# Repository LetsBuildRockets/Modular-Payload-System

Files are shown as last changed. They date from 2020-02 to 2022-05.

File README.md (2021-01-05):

# Cloning

This repo uses submodules. Be sure to clone the submodules as well as the repo:

```sh
git clone https://github.com/LetsBuildRockets/Modular-Payload-System/
cd Modular-Payload-System
git submodule update --init --recursive
```

# Specifications

The Modular Payload System specifications can be found [here](https://github.com/LetsBuildRockets/Modular-Payload-System/blob/master/Hardware/Reference/Specifications.md).

# Modules

A list of modules can be found [here](https://github.com/LetsBuildRockets/Modular-Payload-System/blob/master/ModuleList.md).

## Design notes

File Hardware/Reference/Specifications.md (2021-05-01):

# Modular Payload System Specifications
Revision: Draft

## Overview
These specifications are split into two categories, General Requirements that all module developers shall follow, and a following section that pertains only to modules that meet the High Reliability Requirements (HR)

## Naming Conventions

Bus modules have a basic naming scheme in the format XXX-NNM, for example CPU-010. The prefix letters define the type of module. The two numbers NN define the board number. The last number M, defines the assembly variant. 

| Prefix | Type |
| :----: | :--- |
|  PSU | Power Supply Module. Should also be used for power related modules, if for example, you needed to power external devices from the BUS rails. |
|  DBG | Debug/Development Module |
|  TOP | Top Module. Design to terminate the top of the stack. |
|  BOT | Bottom Module. Design to terminate the bottom of the stack.  |
|  CPU | Flight Computer Module |
| IO | IO board. Includes modules for driving relays, pyros, etc. |
|  BAT | Battery Module. This is any module that generates the +VBAT rail. |
|  AUX | Auxiliary Modules for doing *weird* stuff. |
|  TMP | Template Modules |

## General Specifications
1. Documentation
    1. Module naming shall conform to the naming convention outlined in this document. (This is not required for 3rd party modules, but is required if they will be contributed to LBR's repository.)
    2. Module schematics shall be licensed CC BY-NC 4.0
    3. A compliance matrix shall be filled out. A template one can be generated using by running ```python ./Scripts/generate-compliance-matrix.py ``` from the root directory of this repository. (This is not required for 3rd party modules, but is required if they will be contributed to LBR's repository.)
    4. Modules shall be labeled with a revision letter. (Follow ASME guidelines, Capitol letter A, B, C, ..., Z, AA, AB, etc. The letters I, O, P, Q, S, and Z shall be skipped)
2. Performance
    1. Electrical connectors shall have continuous current carrying capacity derated to 80%.
    2. Ceramic capacitors shall be derated to 60% operating Voltage. Partial non compliance here is acceptable if the derating failure is only due to voltage rail tolerance.
    3. Polymer tantalum capacitors shall be derated to 80% operating Voltage
    4. Polymer tantalums shall be sourced from reputable manufacturers (KEMET, AVX, etc.) No other type of polarized capacitor should be used. (The goal here is to provide safe operation for the entire bus in hot environments and at high altitudes/low pressure. Deviation from this requirement is allowed, but should be done with extreme caution)
    5. Tjmax for all ICs and discrete components should be derated to 80%
    6. All passive electrical components shall be AEC-Q200 qualified
    7. All discrete components shall be AEC-Q101 qualified
    8. All IC should be AEC-Q100 qualified. If the IC is not AEC-Q100 qualified, then it should have a pin compatible/orderable part that is AEC-Q100 qualified. (The goal here is that if the user wants to pay the extra or jump through the purchasing hurdles to actually get an AEC-Q100 part then they can, but it should be the same. For example the ATSAMC21 that is planned for this project has a AEC-Q100 qualified PN suffix, but they are non-stock. We would have to order a full reel. But by using this part, we have the option to simply order the AEC-Q100 part in the future if needed.)
    9. When digital communication and clocks greater than 25.575Mhz are used, the frequency should be chosen such that there are no odd harmonics in the L1 GPS band (1575.42 MHz  +/- 15.345 MHz). Digital frequencies keep out table included for reference below. For example, clock frequencies of 48MHz are not allow because they are between 47.275MHz and 48.205MHz and will produce a 33rd harmonic in the L1 GPS band. 48.25MHz, for example is allowed. If frequencies are used that are in the frequency keep out regions, shielding options should be evaluated in order to prevent conducted or radiated emission from interfering with GPS receivers. If an applications uses GPS other than L1, a frequency keep out table should be made by dividing the the upper and lower bandwidth limits of the band by odd divisors. See [Table 1](#table-1)
    10. Pinout
        1. J1 / P1 bus signal connector shall conform to the pinout located in [Table 4](#table-4)
        2. J2 / P2 bus power connector shall conform to the pinout locate in [Table 5](#table-5)
    11. BUS Power
        1. All power rails shall be connected to both the top and bottom bus connectors, even if the rails are unused on the module.
        2. +VBAT Rail
            1. +VBAT rail shall be 12.8VDC to 34VDC
            2. +VBAT rail steady state current shall be no more than 7.6A
            3. Total +VBAT rail transient current shall be < 1.5x max rated current of 7.6A * 1.5 =  11.4A (this includes inrush or any other transient loads, such as when radios are transmitting, etc.)
            4. Rise time shall be no faster than **TBD** V/s
            5. Rise shall be monotonic
            6. All modules that generate the +VBAT rail via switching regulator topologies shall be 100% tested to ensure conformance to operating voltage requirement. This requirement does not apply to modules that generate the +VBAT rail without active regulation and without power path components that will significantly cause a drop (or increase) in rail voltage.
        3. +12V Rail
            1. +12V rail shall be 11.2VDC to 12.6VDC
            2. +12V rail steady state current shall be no more than 4A
            3. Total +12V rail transient current shall be < 1.5x max rated current of 4A * 1.5=  6A (this includes inrush or any other transient loads, such as when radios are transmitting, etc.)
            4. +12V rail rise time shall be no faster than 10 V/ms
            5. +12V rail rise shall be monotonic
            6. All modules capable of generating the +12V rail shall be 100% tested to ensure conformance to operating voltage requirement 
        4. +5V Rail
            1. +5V rail shall be 4.85V to 5.25V
            2. +5V rail steady state current shall be no more than 3.2A
            3. Total +5V rail transient current shall be < 1.5x max rated current of 3.2A * 1.5=  4.8A (this includes inrush or any other transient loads, such as when radios are transmitting, etc.)
            4. +5V rail rise time shall be no faster than 10 V/ms
            5. +5V rail rise shall be monotonic
            6. All modules capable of generating the +5V rail shall be 100% tested to ensure conformance to operating voltage requirement
        5. +VBAT_Preboot
            1. Reference: Typically, modules don't use this rail.
            2. Reference: Loads on this net will always draw from the battery and will bypass any Under Voltage Lock Out (UVLO). This could damage the battery. Minimize loads on this rail as much as possible. For normal operation, no 3rd party module should be using this rail. Typically, the only load is the +5V_Preboot regulator.
            3. +VBAT_Preboot shall be always on when a battery/power source is connected
            4. +VBAT_Preboot rail shall be 12.8VDC to 34VDC
            5. The +VBAT_Preboot current draw shall be < 1mA (TBR)
            6. All modules capable of generating the +VBAT_Preboot rail shall be 100% tested to ensure conformance to operating voltage requirement
        6. +5V_Preboot
            1. Reference: Typically, modules don't use this rail.
            2. Reference: Loads on this net will always draw from the battery and will bypass any UVLO, which could damage the battery. Minimize loads on this rail as much as possible. For normal operation, no 3rd party module should be using this rail. Typically, the only load is the configurable inverters or active EN switches. For example, the EN switches may use a hall effect sensor that requires 5V and needs to be inverted and could be powered from this rail.
            3. +5V_Preboot shall be always on when a battery/power source is connected
            4. +5V_Preboot rail shall be 4.85V to 5.25V
            5. The +5V_Preboot current draw shall be < 3mA (**TBR**)
            6. All modules capable of generating the +5V_Preboot rail shall be 100% tested to ensure conformance to operating voltage requirement
        7. +5V_Bootstrap
            1. Reference: Typically, modules don't use this rail.
            2. Reference: The +5V_Bootstrap rail is generated by some of the power modules in order to run the microcontrollers during startup. This rail is not guaranteed to be generated by all power modules. Other modules may use this rail if they require +5V before the rest of the bus comes up.
            3. Reference: If this rail is used, it is recommended to OR the +5V_Bootstrap with +5V with diodes on the module. Typically the +5V rail has better conversion efficiency.
            4. +5V_Bootstrap rail shall be 4.85V to 5.25V
            5. The +5V_Bootstrap current draw shall be < 400mA (**TBR**). (Note some power modules my have a +5V_Bootstrap current limit of less than this, so check the datasheet of the specific power supply module you are using if you are going to load this rail.)
            6. All modules capable of generating the +5V_Preboot rail shall be 100% tested to ensure conformance to operating voltage requirement
        8. +0.9V_Reference
            1. Reference: Typically, modules don't use this rail.
            2. Reference: **TBD**
            3. +0.9V_Reference shall be **TBD** to **TBD** V
            4. The +0.9V_Reference current draw shall be < **TBD** mA
            5. All modules capable of generating the +0.9V_Reference rail shall be 100% tested to ensure conformance to operating voltage requirement
    12. BUS Signals
        1. Unused Signals:
            1. All unused signals on the bus shall be passed between J1 and P1. Otherwise the module will break the bus connections!
        2. RFU
            1. RFU, are Reserved for Future Use pins. They shall be connected between J1 and P1. This allows for the signals to be used in the future.
        3. DRAIN
            1. **TBD**
        4. CAN0
            1. **TBD**
        5. CAN1
            1. **TBD**
        6. QSPI
            1. Reference: Typically, modules don't use these signals
            2. **TBD**
            3. The QSPI nets shall be connected to both P1 and J1 to allow for the signals to pass through the module, regardless of if QSPI is used or not.
        7. I2C
            1. Reference: Typically, modules don't use these signals
            2. **TBD**
            3. The I2C nets shall be connected to both P1 and J1 to allow for the signals to pass through the module, regardless of if I2C is used or not.
        8. PPS
            1. Reference: Typically, modules don't use this signal
            2. Reference: The PPS is a precision pulse-per-second provided by GPS receivers. It is not always available on the bus. It will only be provided when there is a GPS-NNM module capable of generating this signal is on the bus, and while it has a GPS lock (or sufficient clock synchronization) 
            3. PPS shall be a one pulse per second pulse (defined by rising edge) and shall have a pulse width of 10ms to 150ms
            4. PPS must be driven through a ~680ohm series resistor.
            5. The PPS net shall be connected to both P1 and J1 to allow for the signal to pass through the module, regardless of if it is used or not.
        9. CTRL_SYNC
            1. Reference: The CTRL_SYNC is used to synchronize software loops between modules. It should be generated by a CPU_NNM module and used by the other modules to kick off their software loop. This sync signal can be divided down if required at the module.
            2. Reference: Most modules that have a microcontroller should have the CTRL_SYNC signal connected to an interrupt capable input pin.
            3. CPU_NNM modules shall output this sync signal on this net.
            4. CTRL_SYNC must be driven through a ~680ohm series resistor.
            5. The start of the control loops should be synchronized with the rising edge of the CTRL_SYNC signal.
            6. Logic high shall be 3.3V +/- 0.3V
            7. Logic low shall be < 0.4V
            8. The CTRL_SYNC frequency shall be 200Hz (**TBR**) at a duty cycle of 48% to 52%.
            9. The CTRL_SYNC net shall be connected to both P1 and J1 to allow for the signal to pass through the module, regardless of if it is used or not.
        10. EN_0, EN_1, EN_2
            1. Reference: Typically, modules don't use these signals, instead you might want to use P_GOOD to enable your module.
            2. Reference: The EN_x signals are active high discrete signals used to enable bus functionality. EN_0, when high, will enable the BAT_NNM boards to supply the +VBAT rail. This allows an external switch on rocket (i.e. a 'remove before flight' tag) to enable the avionics. EN_1 and EN_2 can be used for enabling other functionality. For example, EN_1 could be used with a logical AND gate to enable pyrotechnic charges. This allows for a separate external arming switch, so you can ground test avionics without pyros enabled.
            3. Reference:  These are 5V signals, not 3.3V logic level, so be careful not to connect them directly to a 3.3V microcontroller pin.
            4. Logic high for EN_0, EN_1 and EN_2 shall be +5V +/- 0.5V
            5. Logic low for EN_0, EN_1 and EN_2 shall be < 0.4V.
            6. The current sinked from/sourced to any of the EN_x nets shall be < 1mA.
            7. The current sinked from/sourced to any of the EN_x nets should be < 100uA per module.
            8. EN_0 should be reserved for enabling the +VBAT rail (this will bring up the +12V and +5V rails after a few ms.)
            9. EN_1 **TBD**
            10. EN_2 **TBD**
            11. The EN_0, EN_1 and EN_2 nets shall be connected to both P1 and J1 to allow for the signals to pass through the module, regardless of if it is used or not.
        11. DETECT_A/DETECT_B
             1. Reference: It is recommended that all Modules that have a microcontroller use this detect feature. See [Figure 1](#figure-1) for an example of how this detect signal could be wired up between modules.
             2. Reference: The DETECT_A and DETECT_B signals are used to autodetect the order of the Modules within a stack. This is the only signal in the bus that is not connected to all of the modules in parallel to P1 and J1. DETECT_A is only present on P1 while DETECT_B is only present on J1. DETECT_B should be configured as an input to the microcontroller with a pullup (external or internal to the microcontroller ) When this net is pulled low, the Module should identify itself on the CAN bus. The module will then drive DETECT_A low to request the next module in the stack to identify itself. The bottom board in the stack ties detect to GND to start the detect process. 
             3. If the detect signal is used in the Module, the detect net tied to J1 (top side connector) shall be called DETECT_A and the detect net tied to P1 (bottom side connector) shall be called DETECT_B.
             4. If the detect signal is used in the Module, DETECT_B shall be configured as an input with a pullup resistor between 10kohm and 500kohm to a +3.3V +/- 0.3V supply.
             5. If the detect signal is used in the Module, DETECT_A shall be configured as an open collector/drain output. It shall remain in a hi-z or pullup state (to +3.3V +/- 0.3V) until the module has finished its detect sequence, at which time it will drive the DETECT_A net low (< 0.4V).
             6. If the detect signal is not used in the Module, The net shall tie J1 to P1 and shall be called Detect.
             7. Bottom modules (BOT-NNM) shall tie DETECT_A to GND.
             8. Top modules (TOP-NNM) shall leave DETECT_B floating.
        12. P_GOOD
             1. Reference: The P_GOOD signal is intended to be to power on reset signal for the bus. It can be used to enable local 3.3V LDOs or tied to the rest pin of a microcontroller. This allows the power supplies to come up, then assert the P_GOOD signal in order to enable the rest of the modules. The P_GOOD net is driven through a 220ohm series resistor and a Schottky diode and has a 100kohm pulldown. The goal of the current requirement on this net is to keep the P_GOOD rail from sagging excessively under load. Pulldowns on every module and the Iq of any enable pin may quickly exceed the expected current on this net. The exception the current requirements is reset buttons or other reset features. P_GOOD can be tied low which will draw ~10mA, which will hold the modules in reset.
              2. Reference: Pay close attention to the input pin that P_GOOD drives. For example, if this signal is connected to an input pin of a microcontroller with an ESD diode, and the microcontroller is not powered on during the power on sequence, it could easily draw more than 1.8mA back powering the 3.3V rail.
              3. The P_GOOD signal shall be asserted to 3.3V (2.2V min. 3.6V max.) after VBAT, 12V, and 5V rails have reached operating voltage
              4. The P_GOOD signal shall be de-asserted if any of the rails fall below operating range after ~1ms of persistence
              5. The total amount of current sinked from this net shall be < 1.8 mA during operation.
              6. The total amount of current sinked per module from this net should be < 150uA during operation.
              7. The P_GOOD net shall be connected to both P1 and J1 to allow for the signal to pass through the module, regardless of if it is used or not.
3. Mechanical
    1. Connectors
        1. Top side stacking BUS connectors shall be given ref des J1 and J2 for the signal and power connectors respectively
        2. J1 and J2 shall match in part number.
        3. J1 and J2 shall be part number 10144517-061802LF, 10144517-062802LF, 10144517-063802LF, or 10144517-064802LF
        4. Bottom side stacking BUS connectors shall be given ref des P1 and P2 for the signal and power connectors respectively
        5. P1 and P2 shall be part number 10144518-064802LF
        6. If the Module uses SWD or JTAG for programming, a standard 2x5 0.05" pitch right angle box header should be used as a programming connector. This allows for consistency between modules.
        7. If the Module uses a debug UART, a S4B-ZR(LF)(SN) should be used as a debug UART connector (pin 1: +3.3V, pin 2: GND, pin 3: DEBUG_TX, pin 4: DEBUG_RX). This allows for consistency between modules.
    2. Component Height
        1. Component height limits on the top side of the board are defined by the stacking connectors. See [Table 2](#table-2)
        2. Component height limit on the bottom side of the board is 152 mil      
    3. Stack Height
        1. Reference: Module to Module stack heights are defined by the top side connector. This stack height is defined by the top side of one module to the bottom side of the module above it. i.e. not including board thickness. See [Table 3](#table-3)
    4. Board Outline
        1. Modules should be 1.750" by 1.750" with a 0.125" radius on the corners (This specification may be violated and should be evaluated on a case by case basis.)
    5. Mounting Holes
        1. Modules shall have mounting holes sized for M3 standoffs (126mil nom. drill diameter with a 218mil nom. pad diameter) located at 0.125" from the edge of the 1.75" square
    6. Board thickness
        1. Module PCBs should be 63mil nom. thickness. (This allows for the use of standard standoffs for module stacking. This specification may be violated if alternate standoffs are used)
    7. Test Points
        1. SMT test points should be at least 40mil in diameter
        2. SMT test points should be located on a 0.1" grid on the board. Per **TBD** drawing. (This allows for a standardized pogo pin test board that picks up on this grid. Save from having to create a pogo pin board for each module)
        3. SMT test points should be on top side of the board. (Bottom side test points are allowed, but will be difficult to get to within the stack!)

## High Reliability Specifications

1. Performance
    1. Switching regulators shall have a gain margin of 10dB or greater and a phase margin of 35 degrees or greater
    2. Switching regulators shall have stability performance verified by Monte-Carlo Simulation over load and over component tolerance.
    3. Switching regulators shall have stability performance verified by test at nominal load.
    4. Linear regulators shall have a phase margin of 35 degrees or greater
    5. Linear regulators shall have stability performance verified by test at nominal load.
    6. All ICs and discrete electrical components shall be analyzed to ensure TJ MAX is not exceeded under worst case conditions, or by Monte Carlo

## Tables/Figures
### Table 1
**GPS Frequency Keep outs**

| Harmonic # | Lower (MHz) | Upper (MHz) |
| :---: | :---: | :---: |
| 61 | 25.575 | 26.079 |
| 59 | 26.441 | 26.963 |
| 57 | 27.369 | 27.909 |
| 55 | 28.365 | 28.923 |
| 53 | 29.435 | 30.015 |
| 51 | 30.589 | 31.192 |
| 49 | 31.838 | 32.465 |
| 47 | 33.193 | 33.847 |
| 45 | 34.668 | 35.351 |
| 43 | 36.280 | 36.995 |
| 41 | 38.050 | 38.800 |
| 39 | 40.001 | 40.789 |
| 37 | 42.164 | 42.994 |
| 35 | 44.573 | 45.451 |
| 33 | 47.275 | 48.205 |
| 31 | 50.325 | 51.315 |
| 29 | 53.795 | 54.854 |
| 27 | 57.780 | 58.918 |
| 25 | 62.403 | 63.631 |
| 23 | 67.829 | 69.164 |
| 21 | 74.289 | 75.751 |
| 19 | 82.109 | 83.725 |
| 17 | 91.769 | 93.575 |
| 15 | 104.005 | 106.051 |
| 13 | 120.005 | 122.367 |
| 11 | 141.825 | 144.615 |
| 9 | 173.341 | 176.752 |
| 7 | 222.867 | 227.253 |
| 5 | 312.015 | 318.153 |
| 3 | 520.025 | 530.255 |
| 1 |  1560.075 |  1590.765 |

### Table 2
**Component Clearances**

| Connector PN | Top Side Component Height limit |
| :---: | :---: |
| 10144517-06**1**802LF | 152 mil |
| 10144517-06**2**802LF | 310 mil |
| 10144517-06**3**802LF | 467 mil |
| 10144517-06**4**802LF | 625 mi |

### Table 3
**Module Stack Heights**

| Connector PN | Stack Height | Recommended Standoff |
| :---: | :---: | :---: |
| 10144517-06**1**802LF | 8 mm | M2103-3005-SS |
| 10144517-06**2**802LF | 12 mm | M2107-3005-SS |
| 10144517-06**3**802LF | 16 mm | M2111-3005-SS |
| 10144517-06**4**802LF | 20 mm | M2115-3005-SS |

## Table 4

**J1 / P1 BUS Signal Connector Pinout**

| Signal | Pin # | Pin # | Signal |
| ---: | :---: | :---: | --- |
| DRAIN | 1 | 2 | DRAIN |
| RFU_3 | 3 | 4 | CAN0_N |
| RFU_5 | 5 | 6 | CAN0_N |
| RFU_5 | 7 | 8 | DRAIN |
| RFU_7 | 9 |  10 | CAN1_N |
| RFU_11 |  11 |  12 | CAN1_P |
| RFU_13 |  13 |  14 | DRAIN |
| RFU_15 |  15 |  16 | I2C_SDA |
| RFU_17 |  17 |  18 | I2C_SCL |
| RFU_19 |  19 |  20 | DRAIN |
| RFU_21 |  21 |  22 | PPS |
| RFU_23 |  23 |  24 | DRAIN |
| +5V_Preboot |  25 |  26 | CTRL_SYNC |
| DRAIN |  27 |  28 | DRAIN |
| QSPI_CLK |  29 |  30 | P_GOOD |
| QSPI_IO0 |  31 |  32 | J1: DETECT_A, P1: DETECT_B |
| QSPI_IO1 |  33 |  34 | EN_0 |
| QSPI_IO2 |  35 |  36 | EN_1 |
| QSPI_IO3 |  37 |  38 | EN_2 |
| DRAIN |  39 |  40 | DRAIN |
| SYNC_0 |  41 |  42 | +0.9V_Reference |
| GND |  43 |  44 | +5V_Bootstrap |
| GND |  45 |  46 | +5V |
| GND |  47 |  48 | +5V |
| GND |  49 |  50 | +5V |
| GND |  51 |  52 | +5V |
| GND |  53 |  54 | +5V |
| GND |  55 |  56 | +5V |
| GND |  57 |  58 | +5V |
| GND |  59 |  60 | +5V |

## Table 5

**J2 / P2 BUS Power Connector Pinout**

| Signal | Pin # | Pin # | Signal |
| ---: | :---: | :---: | --- |
| +12V | 1 | 2 | GND |
| +12V | 3 | 4 | GND |
| +12V | 5 | 6 | GND |
| +12V | 7 | 8 | GND |
| +12V | 9 |  10 | GND |
| +12V |  11 |  12 | GND |
| +12V |  13 |  14 | GND |
| +12V |  15 |  16 | GND |
| +12V |  17 |  18 | GND |
| +12V |  19 |  20 | GND |
| +VBAT |  21 |  22 | GND |
| +VBAT |  23 |  24 | GND |
| +VBAT |  25 |  26 | GND |
| +VBAT |  27 |  28 | GND |
| +VBAT |  29 |  30 | GND |
| +VBAT |  31 |  32 | GND |
| +VBAT |  33 |  34 | GND |
| +VBAT |  35 |  36 | GND |
| +VBAT |  37 |  38 | GND |
| +VBAT |  39 |  40 | GND |
| +VBAT |  41 |  42 | GND |
| +VBAT |  43 |  44 | GND |
| +VBAT |  45 |  46 | GND |
| +VBAT |  47 |  48 | GND |
| +VBAT |  49 |  50 | GND |
| +VBAT |  51 |  52 | GND |
| +VBAT |  53 |  54 | GND |
| +VBAT |  55 |  56 | GND |
| +VBAT |  57 |  58 | GND |
| +VBAT_Preboot |  59 |  60 | GND |

### Figure 1

**DETECT_A/DETECT_B Configuration**

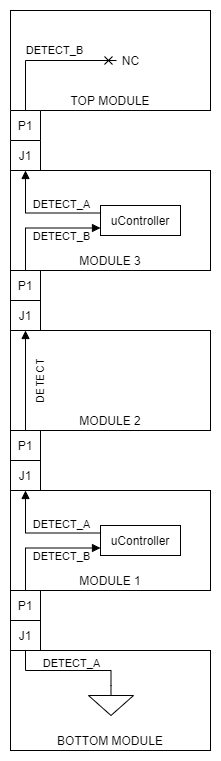
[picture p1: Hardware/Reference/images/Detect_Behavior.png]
Detect Behavior


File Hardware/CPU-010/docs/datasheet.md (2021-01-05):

# CPU-010 Debug/Development Board

## Overview
.

## Specifications
### Operating Conditions
| | Min. | Typ. | Max. | Unit |
| --- | ---- | ---- | ---- | ---- |
| +VBAT | 12.8 | 22 | 34 | V |
| +12V | 11.2 | 12 | 12.6 | V |
| +5V | 4.75 | 5 | 5.25 | V |
| +VBAT Current | | - | - | A |
| +12V Current  | | - | - | A |
| +5V Current | | - | -  | A |

## Configurations
### CPU-011

## Design Notes
### Power Consumption

| Device | PN | Min. | Typ.  | Max.  |
| :---: | :---: | :---: | :---: | :---: |
| U1 | ATSAMV71Q19B-AAB | | | 90mA  |
| U3 | ATA6561-GAQW | 0.01mA | 0.2mA | 0.5mA |
| U4 | ATA6561-GAQW | 0mA (Not in Config.) | 0.2mA | 0.5mA |
| U5 |  IS45S16800F-7TLA2 | 0mA (Not in Config.) | 80mA  | 120mA |
| U8 | KSZ8061RNBV | 0mA (Not in Config.) | | |
| X1 | | | | |
| X2 | MC2016K25.0000C16ESH | 0mA (Not in Config.) |  1mA  |  5mA  |
| SD Card<br/>e.MMC | | 0mA (Not in Config.) | 100mA | 200mA |
| | | | | |
| Total | | | | |

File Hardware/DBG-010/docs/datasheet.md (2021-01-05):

# DBG-010 Debug/Development Board

## Overview
The DBG board is design to allow for basic debug functionality for Modular Payload System (MPS)  modules.

The board provides the following functionality:
- 4mm Banana jacks for powering the bus
- An ATSAMC21G17 microcontroller, with two CAN transceivers, for developing and testing code
- Enable lines broken out (EN_0, EN_1 and EN_2)
- Various jumpers to configure P_GOOD, EN_x, +5V_Bootstrap, and +5V_Preboot

## Specifications
### Operating Conditions
| | Min. | Typ. | Max. | Unit |
| --- | ---- | ---- | ---- | ---- |
| +VBAT | 12.8 | 22 | 34 | V |
| +12V | 11.2 | 12 | 12.6 | V |
| +5V | 4.75 | 5 | 5.25 | V |
| +VBAT Current | | 0.1  | 7.6  | A |
| +12V Current  | | 0.1  | 4 | A |
| +5V Current | | 0.2  | 3.2  | A |

## Configurations
### DBG-011
This configuration has all of the functionality of the board. It has the banana jacks for powering the bus, the enable lines,  P_GOOD, two CAN transceivers, and the ATSAMC21G17.
### DBG-012
Same as DBG-010 but with P1 and P2 installed
### DBG-013
This configuration only has the banana jacks for powering the bus, the enable lines, and P_GOOD. This configuration is designed for simply providing power to the bus
### DBG-014
This configuration only has the banana jacks and top and bottom bus connectors. This configuration is designed to breakout the power connections to measure or load the rails for testing

## Jumpers
- **P5** enables generation of the +5V_Preboot rail from the +5V rail. Jumper pins 1 and 2 to enable. Jumper pins 2 and 3 to disable.
- **P6** enables generation of the +5V_Bootstrap rail from the +5V rail.  Jumper pins 1 and 2 to enable. Jumper pins 2 and 3 to disable.
- **P7** selects the EN signal for the local +3.3V LDO. Jumper pins 1 and 2 to enable the local +3.3V LDO when P_GOOD is high. This matches the functionality of most of the modules. This requires a PSU module to be present. Jumper pins 2 and 3 to enable the +3.3V LDO. Remove the jumper to disable the +3.3V LDO.
- **P21** controls the P_GOOD signal. Jumper pins 1 and 2 to force P_GOOD high. This will enable the rest of the modules on the bus. (Note, this requires the +3.3V regulator to be enabled with P7).  Jumper pins 2 and 3 to allow PSU modules to control P_GOOD. 
- **P22** controls the DETECT_B signal. Jumper pins 1 and 2 to pull DETECT_B low and start the ident process. Jumper pins 2 and 3 to leave this functionality disabled.
- **P9** enables additional termination on CAN0. Install the jumper to enable additional termination, remove the jumper to disable. This allows for somewhat proper operation of the CAN0 bus without using a TOP module.
- **P11** enables additional termination on CAN1. Install the jumper to enable additional termination, remove the jumper to disable. This allows for somewhat proper operation of the CAN1 bus without using a TOP module.
- **P12** selects the EN_0 mode. Jumper pins 1 and 2 to force EN_0 high.  Jumper pins 2 and 3 to allow the external control of EN_0 from P18. (Note, both these modes require +5V_Preboot to be present. Either enable local generation using P5, or use a PSU module)
- **P13** selects the inversion of the EN_0 signal from P18. Jumper pins 1 and 2 to use the P18 EN_0 signal. Jumper pins 2 and 3 to invert the EN_0 signal from P18.
- **P14** selects the EN_1 mode. Jumper pins 1 and 2 to force EN_1 high.  Jumper pins 2 and 3 to allow the external control of EN_1 from P19. (Note, both these modes require +5V_Preboot to be present. Either enable local generation using P5, or use a PSU module)
- **P15** selects the inversion of the EN_1 signal from P19. Jumper pins 1 and 2 to use the P19 EN_1 signal. Jumper pins 2 and 3 to invert the EN_1 signal from P19.
- **P16** selects the EN_2 mode. Jumper pins 1 and 2 to force EN_2 high.  Jumper pins 2 and 3 to allow the external control of EN_2 from P20. (Note, both these modes require +5V_Preboot to be present. Either enable local generation using P5, or use a PSU module)
- **P17** selects the inversion of the EN_2 signal from P20. Jumper pins 1 and 2 to use the P20 EN_2 signal. Jumper pins 2 and 3 to invert the EN_2 signal from P20.

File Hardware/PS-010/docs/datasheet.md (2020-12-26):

# PSU-010 Power Supply Module

## Overview
- 

## Specifications
### Operating Conditions
| | Min. | Typ. | Max. | Unit |
| --- | ---- | ---- | ---- | ---- |
| +VBAT | 12.8 | 22 | 34 | V |
| +12V | | 12 | 1 | V |
| +5V | | 5 | | V |
| +VBAT Current | | | | A |
| +12V Current  | | 0 | | A |
| +5V Current | | | | A |

## Configurations

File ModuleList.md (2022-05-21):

# Module List
|  Module | Revision | Datasheet |
|--- | --- | --- |
| ASBUILT.CSV | - | - | 
| BAT-010 - Battery Module | A (draft) | - | 
| BOB-001 | - | - | 
| CPU-010 - SAM V71 CPU Module<br/>- CPU-011 - - | A (draft) | [datasheet](https://github.com/LetsBuildRockets/Modular-Payload-System/blob/master/Hardware/CPU-010/docs/datasheet.md) | 
| CPUEX-010 - CPU Expansion<br/>- CPUEX-011 - - | A (draft) | - | 
| DBG-010 - Development/Debug Board<br/>- DBG-011 - All debug features<br/>- DBG-012 - All debug features and P1/P2<br/>- DBG-013 - Bus power and various jumpers<br/>- DBG-014 - Banana Jacks only | [A](https://github.com/LetsBuildRockets/Modular-Payload-System/releases/tag/DBG-010-A) | [datasheet](https://github.com/LetsBuildRockets/Modular-Payload-System/blob/master/Hardware/DBG-010/docs/datasheet.md) | 
| DBG-020 - Pogo Pin TP Module<br/>- DBG-021 | [A](https://github.com/LetsBuildRockets/Modular-Payload-System/releases/tag/DBG-020-A) | - | 
| DBG-030 - Pogo Pin Spacer Perf Module | [A](https://github.com/LetsBuildRockets/Modular-Payload-System/releases/tag/DBG-030-A) | - | 
| DBG-040 | - | - | 
| IO-010 | - | - | 
| PS-010 - Power Supply Module 5V/3.2A, 12V/4A<br/>- PS-011 - Power Supply Module<br/>- PS-011_SIM - Power Supply Module | [A](https://github.com/LetsBuildRockets/Modular-Payload-System/releases/tag/PS-010-A) | [datasheet](https://github.com/LetsBuildRockets/Modular-Payload-System/blob/master/Hardware/PS-010/docs/datasheet.md) | 
| TMP-010 - Modular Payload System Template<br/>- TMP-011 | [B](https://github.com/LetsBuildRockets/Modular-Payload-System/releases/tag/TMP-010-B) | - | 
| TOP-010 - Top Module | A (draft) | - | 

This file was autogenerated with /Scripts/generate-module-list.py on 05/21/2022 15:31:53

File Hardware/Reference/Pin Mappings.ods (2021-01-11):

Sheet: TMP-001
Pin(1) | I/O Pin |  |  | B(2,3) | C | D | F | G | Peripheral Assignments
SAM C21G |  | ADC0 | ADC1 | AC | SERCOM(2,3,4) | SERCOM-ALT(4) | TCC | COM | CAN | GPIO | SWD | UART
1 | PA00 |  |  |  |  | SERCOM1/ PAD[0] |  |  |  | CTRL_SYNC
2 | PA01 |  |  |  |  | SERCOM1/ PAD[1]
3 | PA02 | AIN[0] |  | AIN[4]
4 | PA03 | AIN[1] |  | AIN[5]
9 | PA04 | AIN[4] |  | AIN[0] |  | SERCOM0/ PAD[0]
10 | PA05 | AIN[5] |  | AIN[1] |  | SERCOM0/ PAD[1]
11 | PA06 | AIN[6] |  | AIN[2] |  | SERCOM0/ PAD[2]
12 | PA07 | AIN[7] |  | AIN[3] |  | SERCOM0/ PAD[3]
13 | PA08 | AIN[8] | AIN[10] |  | SERCOM0/ PAD[0] | SERCOM2/ PAD[0] | TCC1/ WO[2]
14 | PA09 | AIN[9] | AIN[11] |  | SERCOM0/ PAD[1] | SERCOM2/ PAD[1] | TCC1/ WO[3]
15 | PA10 | AIN[10] |  |  | SERCOM0/ PAD[2] | SERCOM2/ PAD[2] | TCC0/ WO[2]
16 | PA11 | AIN[11] |  |  | SERCOM0/ PAD[3] | SERCOM2/ PAD[3] | TCC0/ WO[3]
21 | PA12 |  |  |  | SERCOM2/ PAD[0] | SERCOM4/ PAD[0] | TCC0/ WO[6] |  |  | DETECT_A
22 | PA13 |  |  |  | SERCOM2/ PAD[1] | SERCOM4/ PAD[1] | TCC0/ WO[7] |  |  | DETECT_B
23 | PA14 |  |  |  | SERCOM2/ PAD[2] | SERCOM4/ PAD[2] | TCC0/ WO[4] |  |  | XTAL
24 | PA15 |  |  |  | SERCOM2/ PAD[3] | SERCOM4/ PAD[3] | TCC0/ WO[5] |  |  | XTAL_NC
25 | PA16 |  |  |  | SERCOM1/ PAD[0] | SERCOM3/ PAD[0] | TCC0/ WO[6] |  |  |  |  | DEBUG_TX
26 | PA17 |  |  |  | SERCOM1/ PAD[1] | SERCOM3/ PAD[1] | TCC0/ WO[7] |  |  |  |  | DEBUG_RX
27 | PA18 |  |  |  | SERCOM1/ PAD[2] | SERCOM3/ PAD[2] | TCC0/ WO[2]
28 | PA19 |  |  |  | SERCOM1/ PAD[3] | SERCOM3/ PAD[3] | TCC0/ WO[3]
29 | PA20 |  |  |  | SERCOM5/ PAD[2] | SERCOM3/ PAD[2] | TCC0/ WO[6]
30 | PA21 |  |  |  | SERCOM5/ PAD[3] | SERCOM3/ PAD[3] | TCC0/ WO[7]
31 | PA22 |  |  |  | SERCOM3/ PAD[0] | SERCOM5/ PAD[0] | TCC0/ WO[4]
32 | PA23 |  |  |  | SERCOM3/ PAD[1] | SERCOM5/ PAD[1] | TCC0/ WO[5]
33 | PA24 |  |  |  | SERCOM3/ PAD[2] | SERCOM5/ PAD[2] | TCC1/ WO[2] | CAN0/TX
34 | PA25 |  |  |  | SERCOM3/ PAD[3] | SERCOM5/ PAD[3] | TCC1/ WO[3] | CAN0/RX
39 | PA27
41 | PA28 |  |  |  |  |  |  |  | CAN0_STBY
45 | PA30 |  |  |  |  | SERCOM1/ PAD[2] |  | CORTEX_M0P/ SWCLK |  |  | SWCLK
46 | PA31 |  |  |  |  | SERCOM1/ PAD[3] |  | CORTEX_M0P/ SWDIO |  |  | SWDIO
47 | PB02 |  | AIN[2] |  |  | SERCOM5/ PAD[0]
48 | PB03 |  | AIN[3] |  |  | SERCOM5/ PAD[1]
7 | PB08 | AIN[2] | AIN[4] |  |  | SERCOM4/ PAD[0]
8 | PB09 | AIN[3] | AIN[5] |  |  | SERCOM4/ PAD[1]
19 | PB10 |  |  |  |  | SERCOM4/ PAD[2] | TCC0/ WO[4] | CAN1/TX
20 | PB11 |  |  |  |  | SERCOM4/ PAD[3] | TCC0/ WO[5] | CAN1/RX
37 | PB22 |  |  |  |  | SERCOM5/ PAD[2] |  | CAN0/TX | CAN0_TX
38 | PB23 |  |  |  |  | SERCOM5/ PAD[3] |  | CAN0/RX | CAN0_RX

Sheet: IO-001
Pin(1) | I/O Pin |  |  | B(2,3) | C | D | G | Peripheral Assignments
SAM C21G |  | ADC0 | ADC1 | AC | SERCOM(2,3,4) | SERCOM-ALT(4) | COM | CAN | Analog | GPIO | SWD
1 | PA00 |  |  |  |  | SERCOM1/ PAD[0]
2 | PA01 |  |  |  |  | SERCOM1/ PAD[1]
3 | PA02 | AIN[0] |  | AIN[4]
4 | PA03 | AIN[1] |  | AIN[5]
9 | PA04 | AIN[4] |  | AIN[0] |  | SERCOM0/ PAD[0]
10 | PA05 | AIN[5] |  | AIN[1] |  | SERCOM0/ PAD[1]
11 | PA06 | AIN[6] |  | AIN[2] |  | SERCOM0/ PAD[2]
12 | PA07 | AIN[7] |  | AIN[3] |  | SERCOM0/ PAD[3]
13 | PA08 | AIN[8] | AIN[10] |  | SERCOM0/ PAD[0] | SERCOM2/ PAD[0]
14 | PA09 | AIN[9] | AIN[11] |  | SERCOM0/ PAD[1] | SERCOM2/ PAD[1]
15 | PA10 | AIN[10] |  |  | SERCOM0/ PAD[2] | SERCOM2/ PAD[2]
16 | PA11 | AIN[11] |  |  | SERCOM0/ PAD[3] | SERCOM2/ PAD[3]
21 | PA12 |  |  |  | SERCOM2/ PAD[0] | SERCOM4/ PAD[0]
22 | PA13 |  |  |  | SERCOM2/ PAD[1] | SERCOM4/ PAD[1] |  |  |  | DETECT_A
23 | PA14 |  |  |  | SERCOM2/ PAD[2] | SERCOM4/ PAD[2] |  |  |  | DETECT_B
24 | PA15 |  |  |  | SERCOM2/ PAD[3] | SERCOM4/ PAD[3]
25 | PA16 |  |  |  | SERCOM1/ PAD[0] | SERCOM3/ PAD[0]
26 | PA17 |  |  |  | SERCOM1/ PAD[1] | SERCOM3/ PAD[1]
27 | PA18 |  |  |  | SERCOM1/ PAD[2] | SERCOM3/ PAD[2]
28 | PA19 |  |  |  | SERCOM1/ PAD[3] | SERCOM3/ PAD[3]
29 | PA20 |  |  |  | SERCOM5/ PAD[2] | SERCOM3/ PAD[2]
30 | PA21 |  |  |  | SERCOM5/ PAD[3] | SERCOM3/ PAD[3]
31 | PA22 |  |  |  | SERCOM3/ PAD[0] | SERCOM5/ PAD[0]
32 | PA23 |  |  |  | SERCOM3/ PAD[1] | SERCOM5/ PAD[1]
33 | PA24 |  |  |  | SERCOM3/ PAD[2] | SERCOM5/ PAD[2] | CAN0/TX | CAN0TX
34 | PA25 |  |  |  | SERCOM3/ PAD[3] | SERCOM5/ PAD[3] | CAN0/RX | CAN0RX
39 | PA27 |  |  |  |  |  |  | CAN0_STBY
41 | PA28 |  |  |  |  |  |  | CAN1_STBY
45 | PA30 |  |  |  |  | SERCOM1/ PAD[2] | CORTEX_M0P/ SWCLK |  |  |  | SWCLK
46 | PA31 |  |  |  |  | SERCOM1/ PAD[3] | CORTEX_M0P/ SWDIO |  |  |  | SWDIO
47 | PB02 |  | AIN[2] |  |  | SERCOM5/ PAD[0]
48 | PB03 |  | AIN[3] |  |  | SERCOM5/ PAD[1]
7 | PB08 | AIN[2] | AIN[4] |  |  | SERCOM4/ PAD[0]
8 | PB09 | AIN[3] | AIN[5] |  |  | SERCOM4/ PAD[1]
19 | PB10 |  |  |  |  | SERCOM4/ PAD[2] | CAN1/TX | CAN1TX
20 | PB11 |  |  |  |  | SERCOM4/ PAD[3] | CAN1/RX | CAN1RX
37 | PB22 |  |  |  |  | SERCOM5/ PAD[2] | CAN0/TX
38 | PB23 |  |  |  |  | SERCOM5/ PAD[3] | CAN0/RX

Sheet: DBG-010
Pin(1) | I/O Pin |  |  | B(2,3) | C | D | G | Peripheral Assignments
SAM C21G |  | ADC0 | ADC1 | AC | SERCOM(2,3,4) | SERCOM-ALT(4) | COM | CAN | Analog | GPIO | SWD | I2C | SPI | UART
1 | PA00 |  |  |  |  | SERCOM1/ PAD[0] |  |  |  | CTRL_SYNC
2 | PA01 |  |  |  |  | SERCOM1/ PAD[1]
3 | PA02 | AIN[0] |  | AIN[4]
4 | PA03 | AIN[1] |  | AIN[5]
9 | PA04 | AIN[4] |  | AIN[0] |  | SERCOM0/ PAD[0] |  |  |  |  |  |  |  | UART_TX
10 | PA05 | AIN[5] |  | AIN[1] |  | SERCOM0/ PAD[1] |  |  |  |  |  |  |  | UART_RX
11 | PA06 | AIN[6] |  | AIN[2] |  | SERCOM0/ PAD[2]
12 | PA07 | AIN[7] |  | AIN[3] |  | SERCOM0/ PAD[3]
13 | PA08 | AIN[8] | AIN[10] |  | SERCOM0/ PAD[0] | SERCOM2/ PAD[0] |  |  |  |  |  |  | SPI_MISO_R
14 | PA09 | AIN[9] | AIN[11] |  | SERCOM0/ PAD[1] | SERCOM2/ PAD[1]
15 | PA10 | AIN[10] |  |  | SERCOM0/ PAD[2] | SERCOM2/ PAD[2] |  |  |  |  |  |  | SPI_MOSI_R
16 | PA11 | AIN[11] |  |  | SERCOM0/ PAD[3] | SERCOM2/ PAD[3] |  |  |  |  |  |  | SPI_SCK_R
21 | PA12 |  |  |  | SERCOM2/ PAD[0] | SERCOM4/ PAD[0] |  |  |  | DETECT_A
22 | PA13 |  |  |  | SERCOM2/ PAD[1] | SERCOM4/ PAD[1] |  |  |  | DETECT_B
23 | PA14 |  |  |  | SERCOM2/ PAD[2] | SERCOM4/ PAD[2] |  |  |  | XTAL
24 | PA15 |  |  |  | SERCOM2/ PAD[3] | SERCOM4/ PAD[3] |  |  |  | XTAL_NC
25 | PA16 |  |  |  | SERCOM1/ PAD[0] | SERCOM3/ PAD[0] |  |  |  |  |  | I2C_SDA
26 | PA17 |  |  |  | SERCOM1/ PAD[1] | SERCOM3/ PAD[1] |  |  |  |  |  | I2C_SCL
27 | PA18 |  |  |  | SERCOM1/ PAD[2] | SERCOM3/ PAD[2] |  |  |  |  |  |  |  | DEBUG_TX
28 | PA19 |  |  |  | SERCOM1/ PAD[3] | SERCOM3/ PAD[3] |  |  |  |  |  |  |  | DEBUG_RX
29 | PA20 |  |  |  | SERCOM5/ PAD[2] | SERCOM3/ PAD[2]
30 | PA21 |  |  |  | SERCOM5/ PAD[3] | SERCOM3/ PAD[3]
31 | PA22 |  |  |  | SERCOM3/ PAD[0] | SERCOM5/ PAD[0]
32 | PA23 |  |  |  | SERCOM3/ PAD[1] | SERCOM5/ PAD[1]
33 | PA24 |  |  |  | SERCOM3/ PAD[2] | SERCOM5/ PAD[2] | CAN0/TX
34 | PA25 |  |  |  | SERCOM3/ PAD[3] | SERCOM5/ PAD[3] | CAN0/RX
39 | PA27 |  |  |  |  |  |  | CAN1_STBY
41 | PA28 |  |  |  |  |  |  | CAN0_STBY
45 | PA30 |  |  |  |  | SERCOM1/ PAD[2] | CORTEX_M0P/ SWCLK |  |  |  | SWCLK
46 | PA31 |  |  |  |  | SERCOM1/ PAD[3] | CORTEX_M0P/ SWDIO |  |  |  | SWDIO
47 | PB02 |  | AIN[2] |  |  | SERCOM5/ PAD[0]
48 | PB03 |  | AIN[3] |  |  | SERCOM5/ PAD[1]
7 | PB08 | AIN[2] | AIN[4] |  |  | SERCOM4/ PAD[0]
8 | PB09 | AIN[3] | AIN[5] |  |  | SERCOM4/ PAD[1]
19 | PB10 |  |  |  |  | SERCOM4/ PAD[2] | CAN1/TX | CAN1TX
20 | PB11 |  |  |  |  | SERCOM4/ PAD[3] | CAN1/RX | CAN1RX
37 | PB22 |  |  |  |  | SERCOM5/ PAD[2] | CAN0/TX | CAN0TX
38 | PB23 |  |  |  |  | SERCOM5/ PAD[3] | CAN0/RX | CAN0RX
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

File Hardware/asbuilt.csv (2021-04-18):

Part Number | Revision | SN | as built changes
PS-011 | A | 1 | R13, R23 – ERJ-3EKF1004V instead of ERJ-PB6B1004V U3 – ATA6561-GAQW-N instead of ATA6561-GAQW

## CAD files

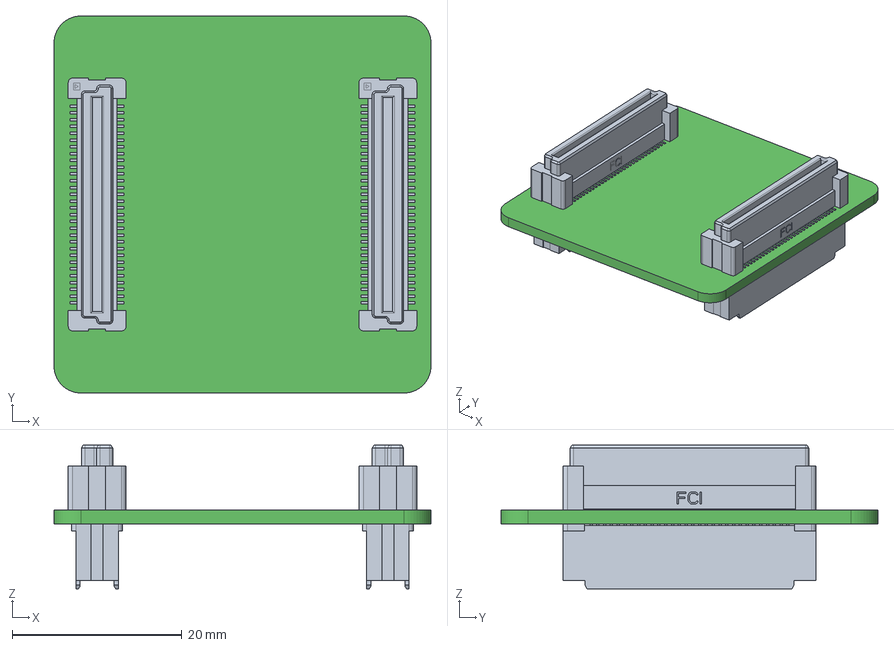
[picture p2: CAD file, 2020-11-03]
Hardware/DBG-040/Sources/Outputs/ExportSTEP/DBG-040.step
44.4 x 44.4 x 16.9 mm
Board
10144518-064x0xxx x 2
10144517-062x0xxx x 2

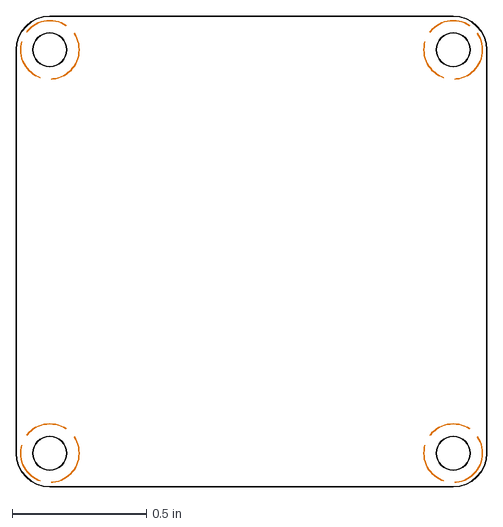
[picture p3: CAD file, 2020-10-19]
Hardware/Reference/Outline.dxf
1.75 x 1.75 in

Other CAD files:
Hardware/Reference/Outline.ipt

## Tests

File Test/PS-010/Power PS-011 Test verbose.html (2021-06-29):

In [1]:

import numpy as np
import time
from ds1054z import DS1054Z
%matplotlib inline
import matplotlib.pyplot as plt
from scipy.signal import blackmanharris
from matplotlib.ticker import EngFormatter
from scipy import signal
from IPython.display import Markdown, display

scope = DS1054Z('192.168.1.252')
print(scope.idn)

def printmd(string, color=None):
    if color != None:
        string = "<span style='color:{}'>{}</span>".format(color, string)
    display(Markdown(string))

RIGOL TECHNOLOGIES,DS1054Z,DS1ZA192409533,00.04.04.SP3

In [2]:

def check_monotonicity_rise(time_data, voltage_data, threshold, window_len_0=301, window_len_1=901):
    voltage_data_filtered = signal.savgol_filter(voltage_data, window_length=window_len_0, polyorder=2, delta=(time_data[1]-time_data[0]))
    fig, ax = plt.subplots()
    ax.plot(time_data, voltage_data) 
    ax.plot(time_data, voltage_data_filtered) 
    formatter = EngFormatter(unit='s')
    ax.xaxis.set_major_formatter(formatter)
    plt.xlabel('Time')
    plt.ylabel('Volts')
    
    dvdt = signal.savgol_filter(voltage_data, window_length=window_len_1, polyorder=2, deriv=1, delta=(time_data[1]-time_data[0]))*1e-3

    fig, ax = plt.subplots(2,figsize=(10,8), dpi=100)
    nmon = dvdt < threshold
    errors_x = []
    errors_y = []
    for x in range(0,len(nmon)):
        if nmon[x]:
            errors_x.append(time_data[x])
            errors_y.append(voltage_data_filtered[x])

    ax[0].plot(errors_x,errors_y,'.', color='lightcoral', markersize=20) 
    ax[0].plot(time_data,voltage_data_filtered)
    ax[0].set(ylabel='Volts')
    ax[1].axhline(threshold, color='lightcoral')
    ax[1].plot(time_data,dvdt) 
    ax[1].set(ylabel='Volts/ms')
    formatter = EngFormatter(unit='s')
    ax[0].xaxis.set_major_formatter(formatter)
    ax[1].xaxis.set_major_formatter(formatter)
    plt.xlabel('Time')
    
    return min(dvdt)

In [3]:

reqnum = '2.11.4.5'
printmd("### {}".format(reqnum))
printmd("**Checking {} - +5V rail rise shall be monotonic**".format(reqnum))
print("Setting up scope for checking rising monotonicity...")
scope.run()
scope.display_only_channel(1)
scope.set_probe_ratio(1,1)
scope.memory_depth = 120e3
scope.timebase_scale = 1e-3
scope.timebase_offset = 0
scope.set_channel_scale(1,1)
scope.set_channel_offset(1,-3)
scope.write(':TRIGger:MODE EDGE')
scope.write(':TRIGger:COUPling DC')
scope.write(':TRIGger:EDGe:SOURce CHANnel1')
scope.write(':TRIGger:EDGe:SLOPe POSitive')
scope.write(':TRIGger:EDGe:LEVel 2.5')
scope.single()
time.sleep(1)
print("Scope setup. Waiting for trigger.")
while(scope.running):
    time.sleep(1)
print("Triggered!")

print("Grabbing scope data...")
V1 = scope.get_waveform_samples(1,mode='MAX')
Ts1 = scope.waveform_time_values
print("Grabbed scope data!")

monotonic_threshold = -0.5 # V/ms

minimum_slew = check_monotonicity_rise(Ts1, V1, threshold=monotonic_threshold)

print('Maximum Negative slew is {:.2f} V/ms'.format(minimum_slew))

if(minimum_slew > monotonic_threshold):
    printmd('{} - PASSED'.format(reqnum), color='Green')
else:
    printmd('{} - FAILED'.format(reqnum), color='Red')

plt.show()

### 2.11.4.5¶

Checking 2.11.4.5 - +5V rail rise shall be monotonic

Setting up scope for checking rising monotonicity...
Scope setup. Waiting for trigger.
Triggered!
Grabbing scope data...
Grabbed scope data!
Maximum Negative slew is -0.12 V/ms

2.11.4.5 - PASSED

In [4]:

reqnum = '2.11.4.4'
printmd("### {}".format(reqnum))
printmd("**Checking 2.11.4.4 - +5V rail rise time shall be no faster than 10 V/ms**")
rise_slew_rate = float(scope.query(':MEASure:ITEM? PSLEWrate,CHANnel1'))
print('+5V Rail rise slew rate is {:.1f} V/s'.format(rise_slew_rate))
if(minimum_slew < 10e3):
    printmd('{} - PASSED'.format(reqnum), color='Green')
else:
    printmd('{} - FAILED'.format(reqnum), color='Red')

### 2.11.4.4¶

Checking 2.11.4.4 - +5V rail rise time shall be no faster than 10 V/ms

+5V Rail rise slew rate is 1186.8 V/s

2.11.4.4 - PASSED

In [5]:

reqnum = '2.11.3.5'
printmd('### {}'.format(reqnum))
printmd("**Checking {}- +12V rail rise shall be monotonic**".format(reqnum))
print("Setting up scope for checking rising monotonicity...")
scope.run()
scope.display_only_channel(1)
scope.set_probe_ratio(1,1)
scope.memory_depth = 120e3
scope.timebase_scale = 1e-3
scope.timebase_offset = 0
scope.set_channel_scale(1,2)
scope.set_channel_offset(1,-6)
scope.write(':TRIGger:MODE EDGE')
scope.write(':TRIGger:COUPling DC')
scope.write(':TRIGger:EDGe:SOURce CHANnel1')
scope.write(':TRIGger:EDGe:SLOPe POSitive')
scope.write(':TRIGger:EDGe:LEVel 5')
scope.single()
time.sleep(1)
print("Scope setup. Waiting for trigger.")
while(scope.running):
    time.sleep(1)
print("Triggered!")

print("Grabbing scope data...")
V1 = scope.get_waveform_samples(1,mode='MAX')
Ts1 = scope.waveform_time_values
print("Grabbed scope data!")

monotonic_threshold = -0.5 # V/ms

minimum_slew = check_monotonicity_rise(Ts1, V1, threshold=monotonic_threshold)

print('Maximum Negative slew is {:.2f} V/ms'.format(minimum_slew))

if(minimum_slew > monotonic_threshold):
    printmd('{} - PASSED'.format(reqnum), color='Green')
else:
    printmd('{} - FAILED'.format(reqnum), color='Red')

plt.show()

### 2.11.3.5¶

Checking 2.11.3.5- +12V rail rise shall be monotonic

Setting up scope for checking rising monotonicity...
Scope setup. Waiting for trigger.
Triggered!
Grabbing scope data...
Grabbed scope data!
Maximum Negative slew is -0.24 V/ms

2.11.3.5 - PASSED

In [6]:

reqnum = '2.11.3.4'
printmd('### {}'.format(reqnum))
printmd('**Checking {} - +12V rail rise time shall be no faster than 10 V/ms**'.format(reqnum))
rise_slew_rate = float(scope.query(':MEASure:ITEM? PSLEWrate,CHANnel1'))
print('+12V Rail rise slew rate is {:.1f} V/s'.format(rise_slew_rate))
if(minimum_slew < 10e3):
    printmd('{} - PASSED'.format(reqnum), color='Green')
else:
    printmd('{} - FAILED'.format(reqnum), color='Red')

### 2.11.3.4¶

Checking 2.11.3.4 - +12V rail rise time shall be no faster than 10 V/ms

+12V Rail rise slew rate is 2753.6 V/s

2.11.3.4 - PASSED

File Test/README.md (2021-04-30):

generate report using: ``` jupyter nbconvert --to pdf --no-input [notebook].ipynb```

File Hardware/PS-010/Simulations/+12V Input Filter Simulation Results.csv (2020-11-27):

fr | qf | z_out
7.56E+04 | 1.31E+00 | 1.36E-01
8.46E+04 | 1.25E+00 | 1.41E-01
7.55E+04 | 1.23E+00 | 1.44E-01
9.52E+04 | 1.20E+00 | 1.42E-01
7.23E+04 | 1.23E+00 | 1.41E-01
1.14E+05 | 1.14E+00 | 1.34E-01
6.60E+04 | 1.21E+00 | 1.52E-01
8.14E+04 | 1.18E+00 | 1.46E-01
9.08E+04 | 1.09E+00 | 1.61E-01
7.90E+04 | 1.09E+00 | 1.61E-01
6.59E+04 | 1.37E+00 | 1.27E-01
1.09E+05 | 1.26E+00 | 1.28E-01
9.10E+04 | 1.23E+00 | 1.39E-01
6.90E+04 | 1.24E+00 | 1.52E-01
6.59E+04 | 1.18E+00 | 1.62E-01
1.15E+05 | 1.17E+00 | 1.32E-01
7.57E+04 | 1.24E+00 | 1.47E-01
7.93E+04 | 1.20E+00 | 1.47E-01
1.15E+05 | 1.07E+00 | 1.49E-01
1.14E+05 | 1.08E+00 | 1.52E-01
9.10E+04 | 1.27E+00 | 1.30E-01
8.70E+04 | 1.28E+00 | 1.28E-01
7.55E+04 | 1.29E+00 | 1.36E-01
7.93E+04 | 1.27E+00 | 1.46E-01
1.03E+05 | 1.15E+00 | 1.33E-01
7.56E+04 | 1.16E+00 | 1.53E-01
8.68E+04 | 1.12E+00 | 1.52E-01
7.22E+04 | 1.14E+00 | 1.60E-01
9.38E+04 | 1.10E+00 | 1.55E-01
9.55E+04 | 1.07E+00 | 1.53E-01
9.94E+04 | 1.27E+00 | 1.25E-01
7.58E+04 | 1.33E+00 | 1.33E-01
7.90E+04 | 1.30E+00 | 1.31E-01
7.24E+04 | 1.28E+00 | 1.36E-01
6.59E+04 | 1.23E+00 | 1.43E-01
6.57E+04 | 1.20E+00 | 1.56E-01
1.04E+05 | 1.17E+00 | 1.41E-01
1.20E+05 | 1.09E+00 | 1.50E-01
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

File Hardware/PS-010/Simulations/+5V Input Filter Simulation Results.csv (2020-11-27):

fr | qf | z_out
5.24E+04 | 1.33E+00 | 1.63E-01
6.41E+04 | 1.30E+00 | 1.50E-01
7.06E+04 | 1.23E+00 | 1.60E-01
5.74E+04 | 1.21E+00 | 1.79E-01
5.99E+04 | 1.31E+00 | 1.60E-01
6.43E+04 | 1.17E+00 | 1.78E-01
7.54E+04 | 1.09E+00 | 1.77E-01
6.28E+04 | 1.12E+00 | 1.85E-01
6.55E+04 | 1.09E+00 | 1.94E-01
5.60E+04 | 1.14E+00 | 1.86E-01
5.87E+04 | 1.28E+00 | 1.58E-01
7.88E+04 | 1.23E+00 | 1.53E-01
7.71E+04 | 1.22E+00 | 1.59E-01
5.72E+04 | 1.27E+00 | 1.60E-01
6.00E+04 | 1.21E+00 | 1.64E-01
6.43E+04 | 1.16E+00 | 1.88E-01
5.72E+04 | 1.22E+00 | 1.77E-01
5.48E+04 | 1.21E+00 | 1.75E-01
7.73E+04 | 1.11E+00 | 1.72E-01
6.70E+04 | 1.07E+00 | 2.00E-01
6.86E+04 | 1.28E+00 | 1.52E-01
5.73E+04 | 1.25E+00 | 1.76E-01
6.70E+04 | 1.19E+00 | 1.69E-01
5.56E+04 | 1.28E+00 | 1.57E-01
5.48E+04 | 1.23E+00 | 1.61E-01
6.88E+04 | 1.17E+00 | 1.72E-01
5.84E+04 | 1.16E+00 | 1.79E-01
5.86E+04 | 1.19E+00 | 1.80E-01
5.36E+04 | 1.18E+00 | 1.83E-01
6.05E+04 | 1.08E+00 | 1.85E-01
6.41E+04 | 1.29E+00 | 1.56E-01
5.46E+04 | 1.27E+00 | 1.67E-01
5.74E+04 | 1.23E+00 | 1.73E-01
6.74E+04 | 1.24E+00 | 1.54E-01
5.87E+04 | 1.25E+00 | 1.67E-01
7.19E+04 | 1.12E+00 | 1.75E-01
7.56E+04 | 1.15E+00 | 1.68E-01
7.37E+04 | 1.11E+00 | 1.72E-01
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

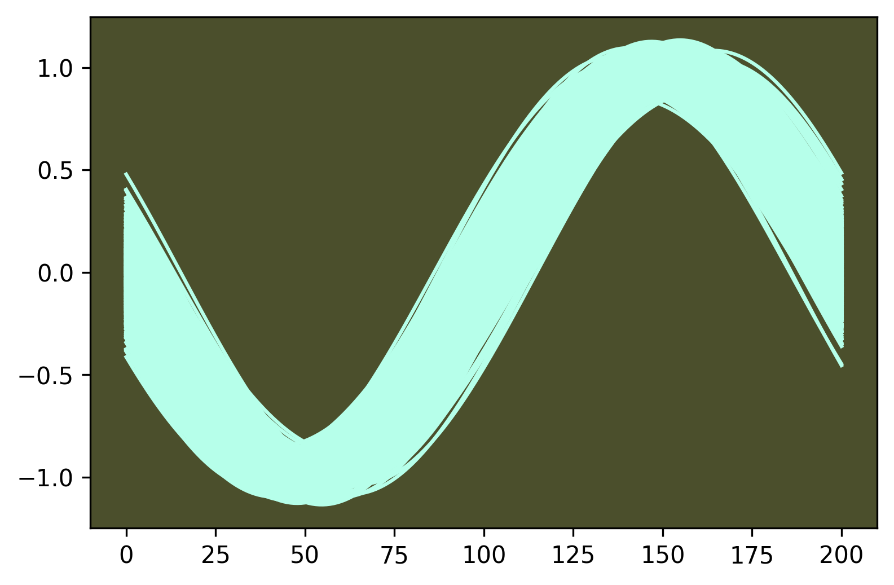
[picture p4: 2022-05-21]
Test/testbench/INST_Drivers/pandas_m.png

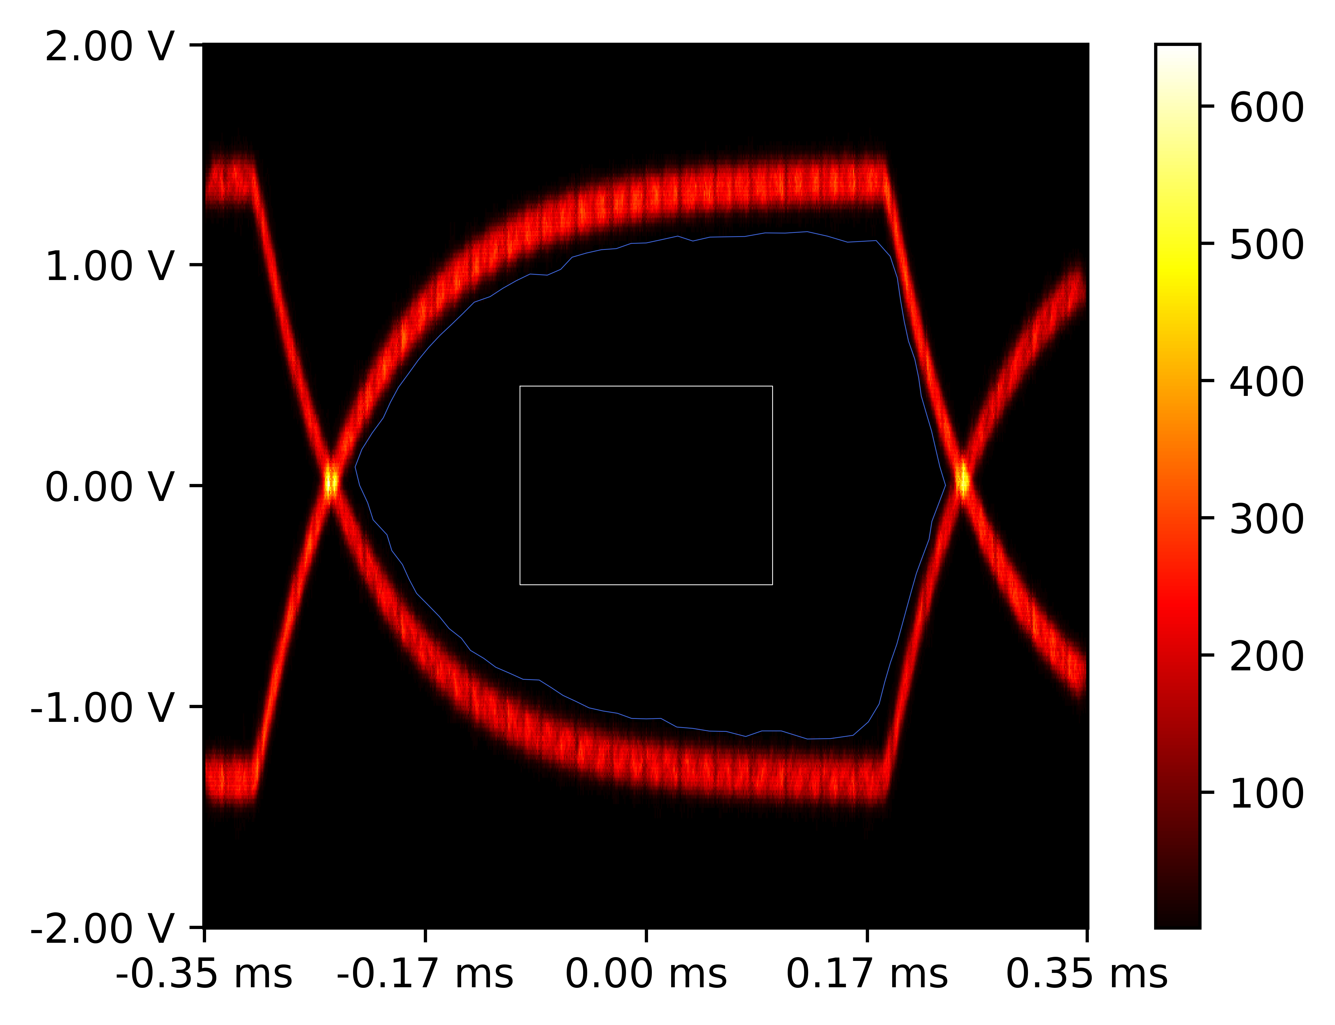
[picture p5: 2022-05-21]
Test/testbench/INST_Drivers/hand_made_persistence.png

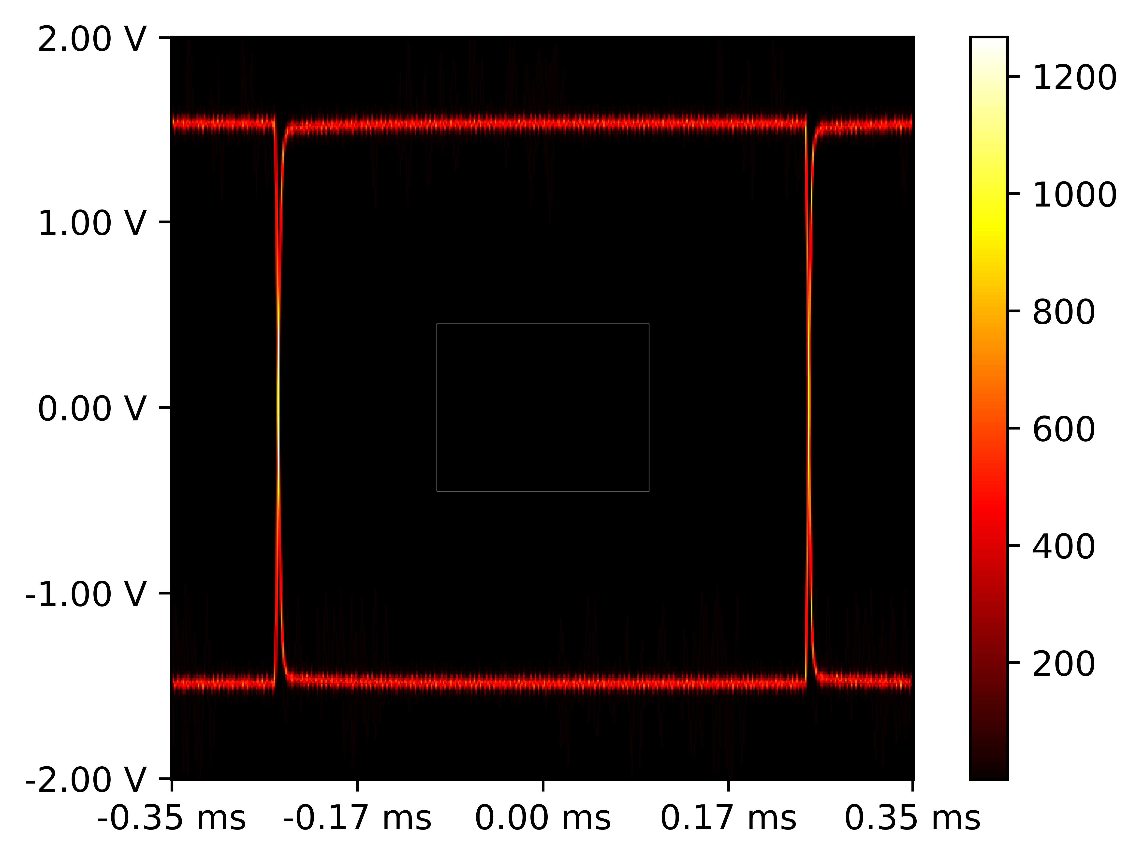
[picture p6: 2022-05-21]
Test/testbench/INST_Drivers/hand_made_persistence - Copy (2).png

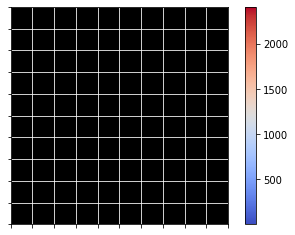
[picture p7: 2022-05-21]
Test/testbench/INST_Drivers/eye-diagram.png

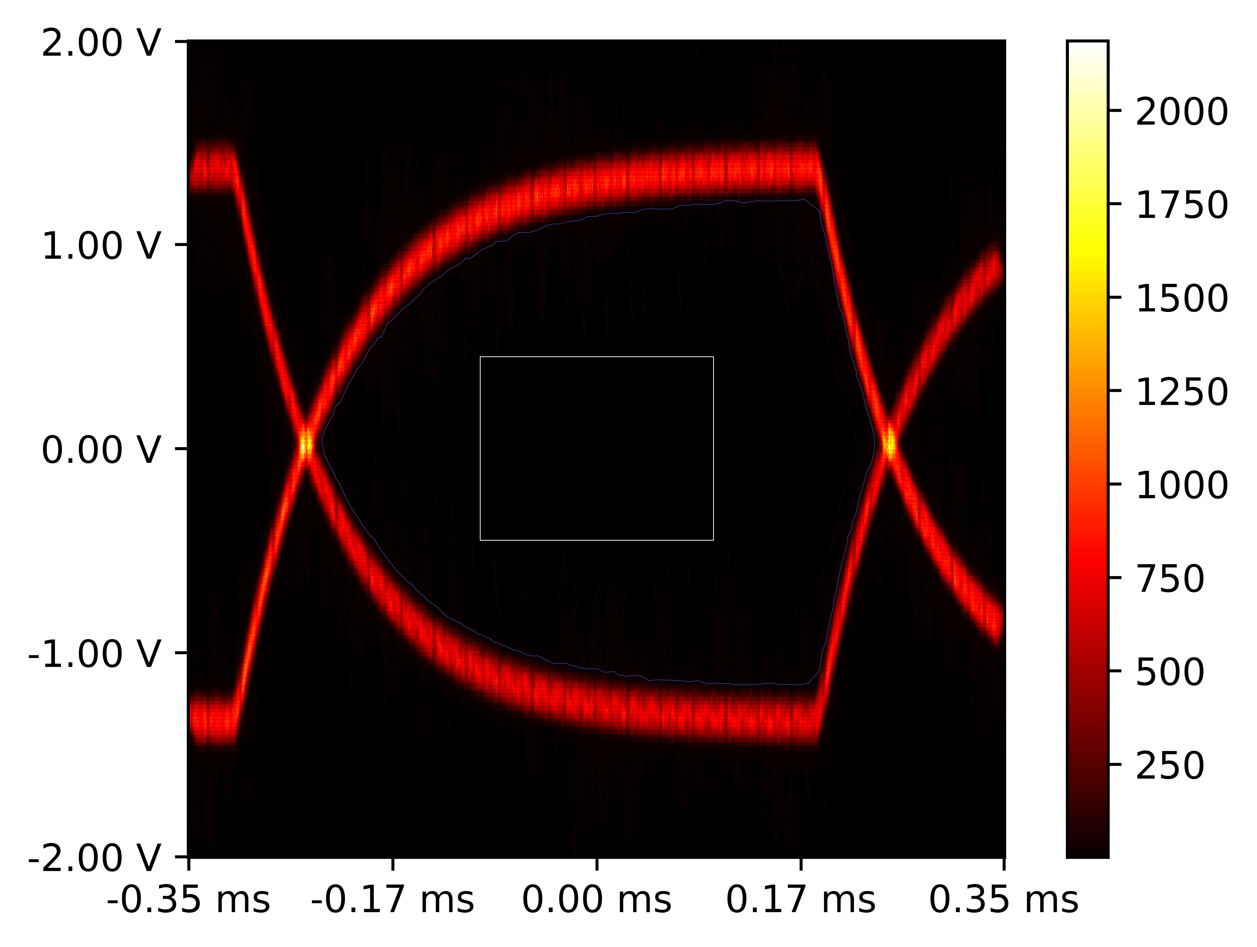
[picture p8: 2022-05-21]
Test/testbench/INST_Drivers/eye.png

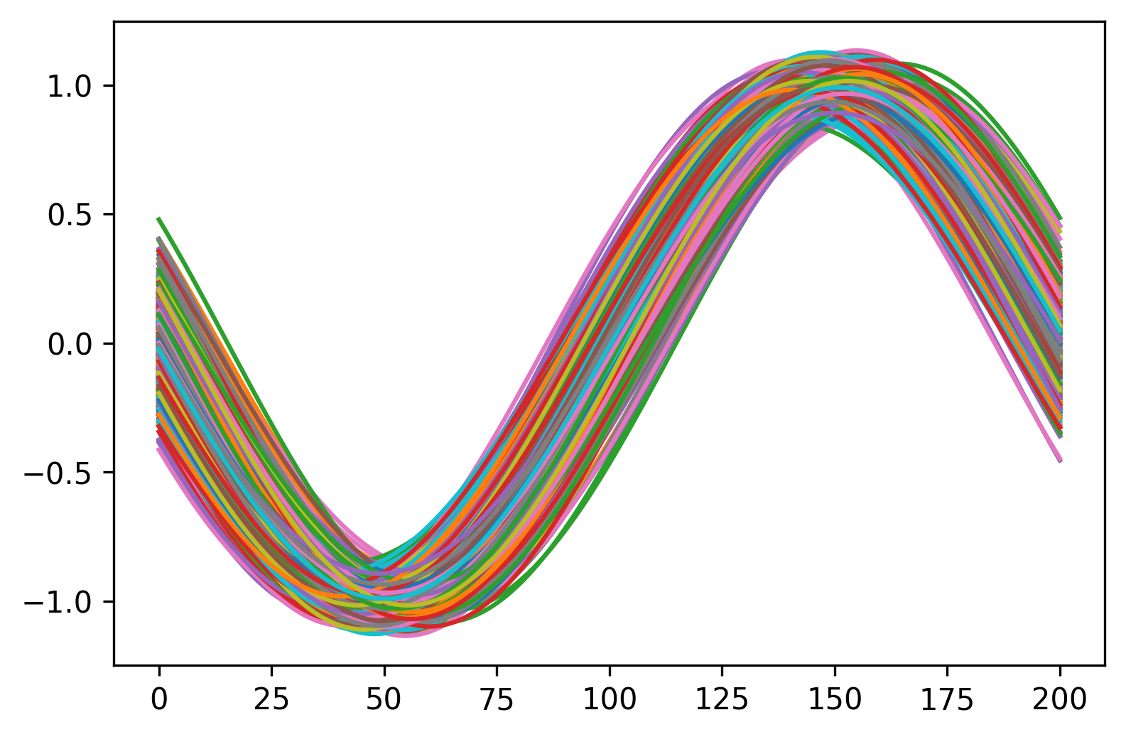
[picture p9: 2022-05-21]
Test/testbench/INST_Drivers/pandas.png

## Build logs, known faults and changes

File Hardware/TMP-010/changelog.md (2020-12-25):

# TMP-010 Change Log

## A.1

- Initial Release

## B

- Changed from Circuit studio to Altium
- Added variants
- Changed naming from TMP-001 to TMP-010, where first two digits represent the board number, and the last is the assembly variant
- Updated title block to include variants and template version
- Changed project parameters to start with the Project prefix
- Updated PNs to incude full orderable PN
- **Updated component height clearances**
- **Changed RFU_25 to +5V_Preboot rail**
- **Renamed +VBAT_Bootstrap to +VBAT_Preboot**

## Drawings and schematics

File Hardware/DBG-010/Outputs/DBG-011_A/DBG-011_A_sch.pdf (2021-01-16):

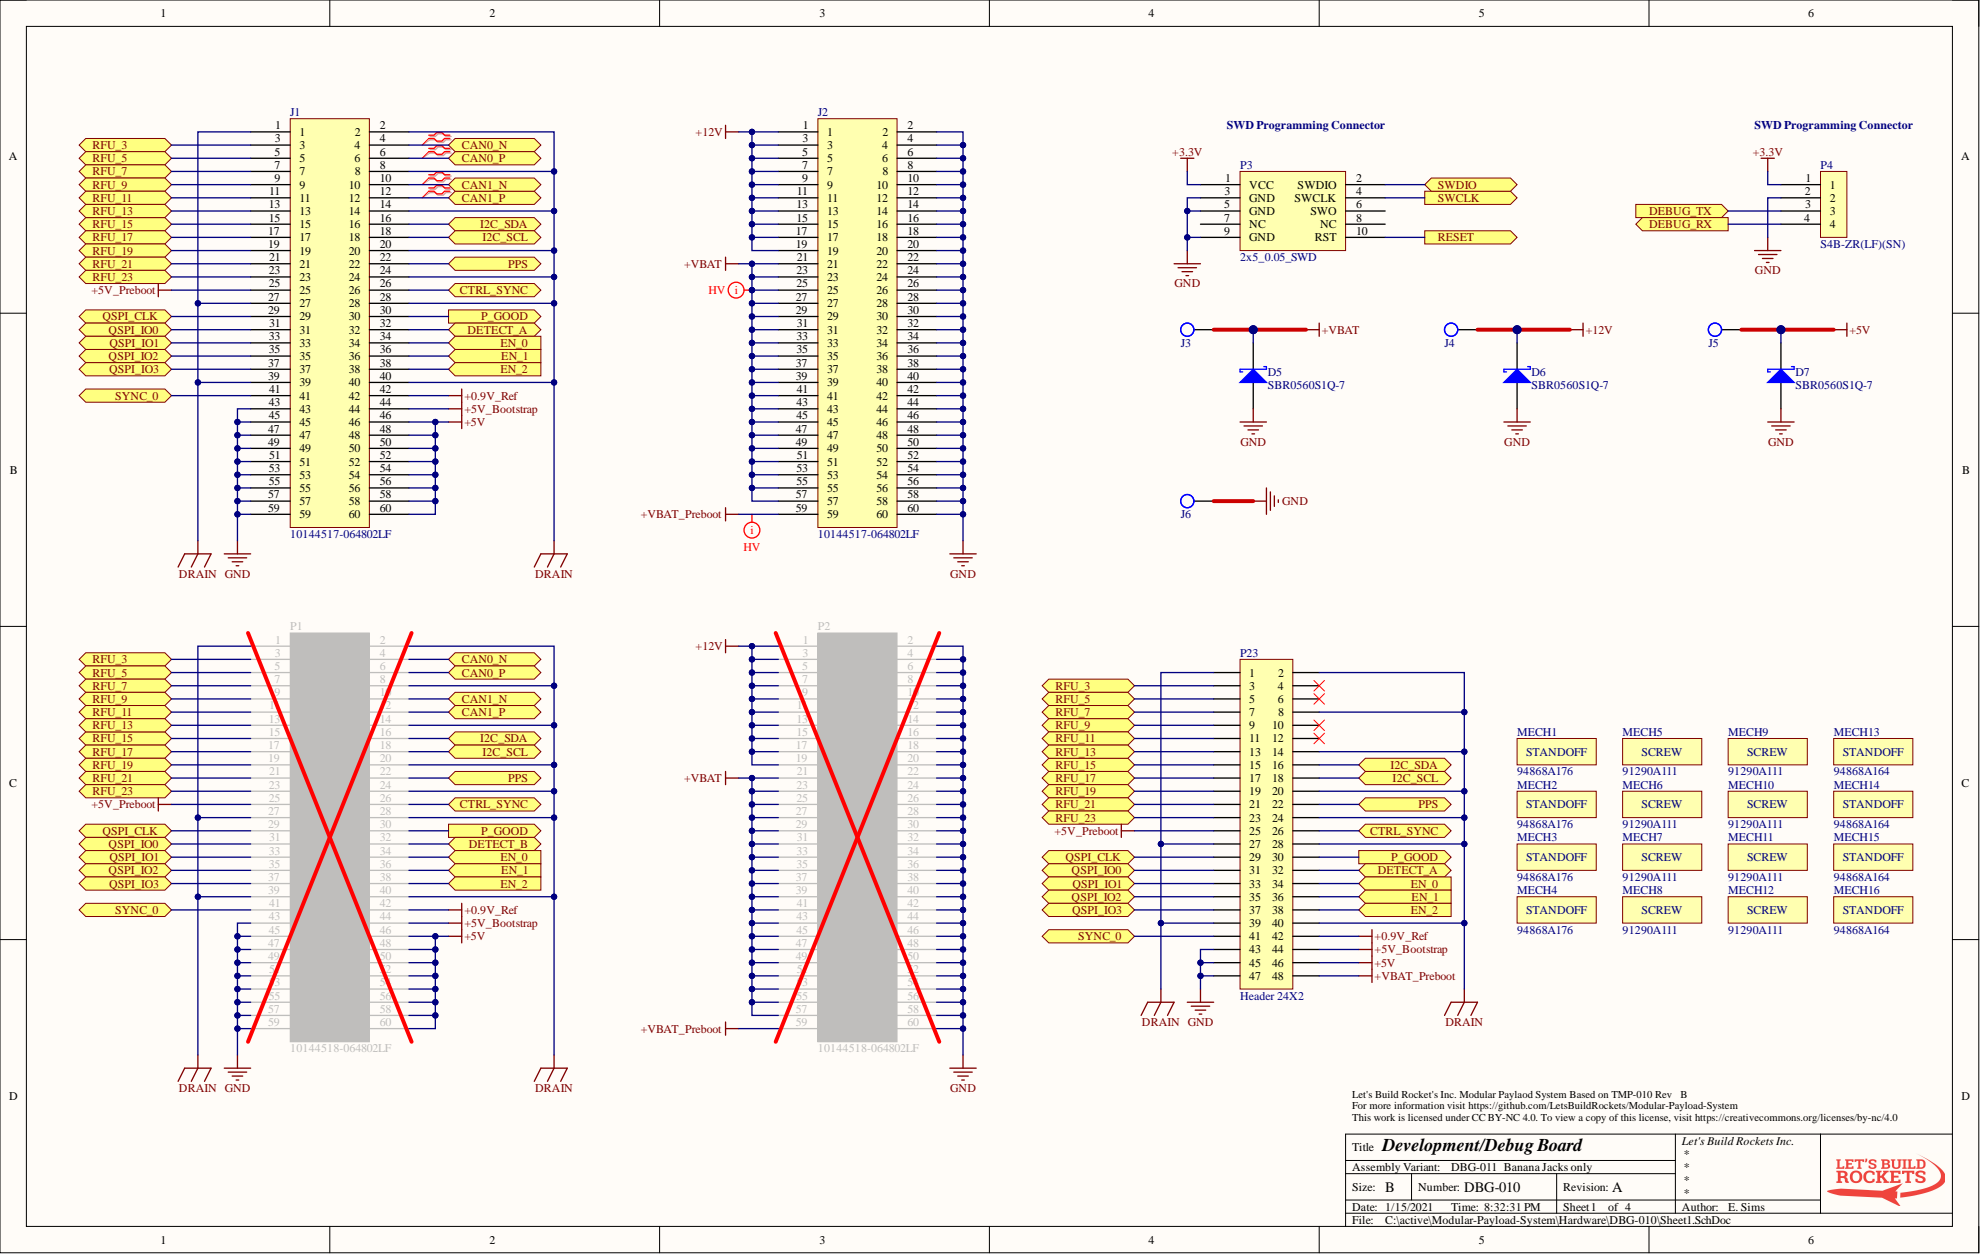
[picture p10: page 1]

Let's Build Rocket's Inc. Modular Paylaod System Based on TMP-010 Rev
For more information visit https://github.com/LetsBuildRockets/Modular-Payload-System
This work is licensed under CC BY-NC 4.0. To view a copy of this license, visit https://creativecommons.org/licenses/by-nc/4.0
Development/Debug Board
Title
Assembly Variant: DBG-011
C:\active\Modular-Payload-System\Hardware\DBG-010\Sheet1.SchDoc

Let's Build Rockets Inc.

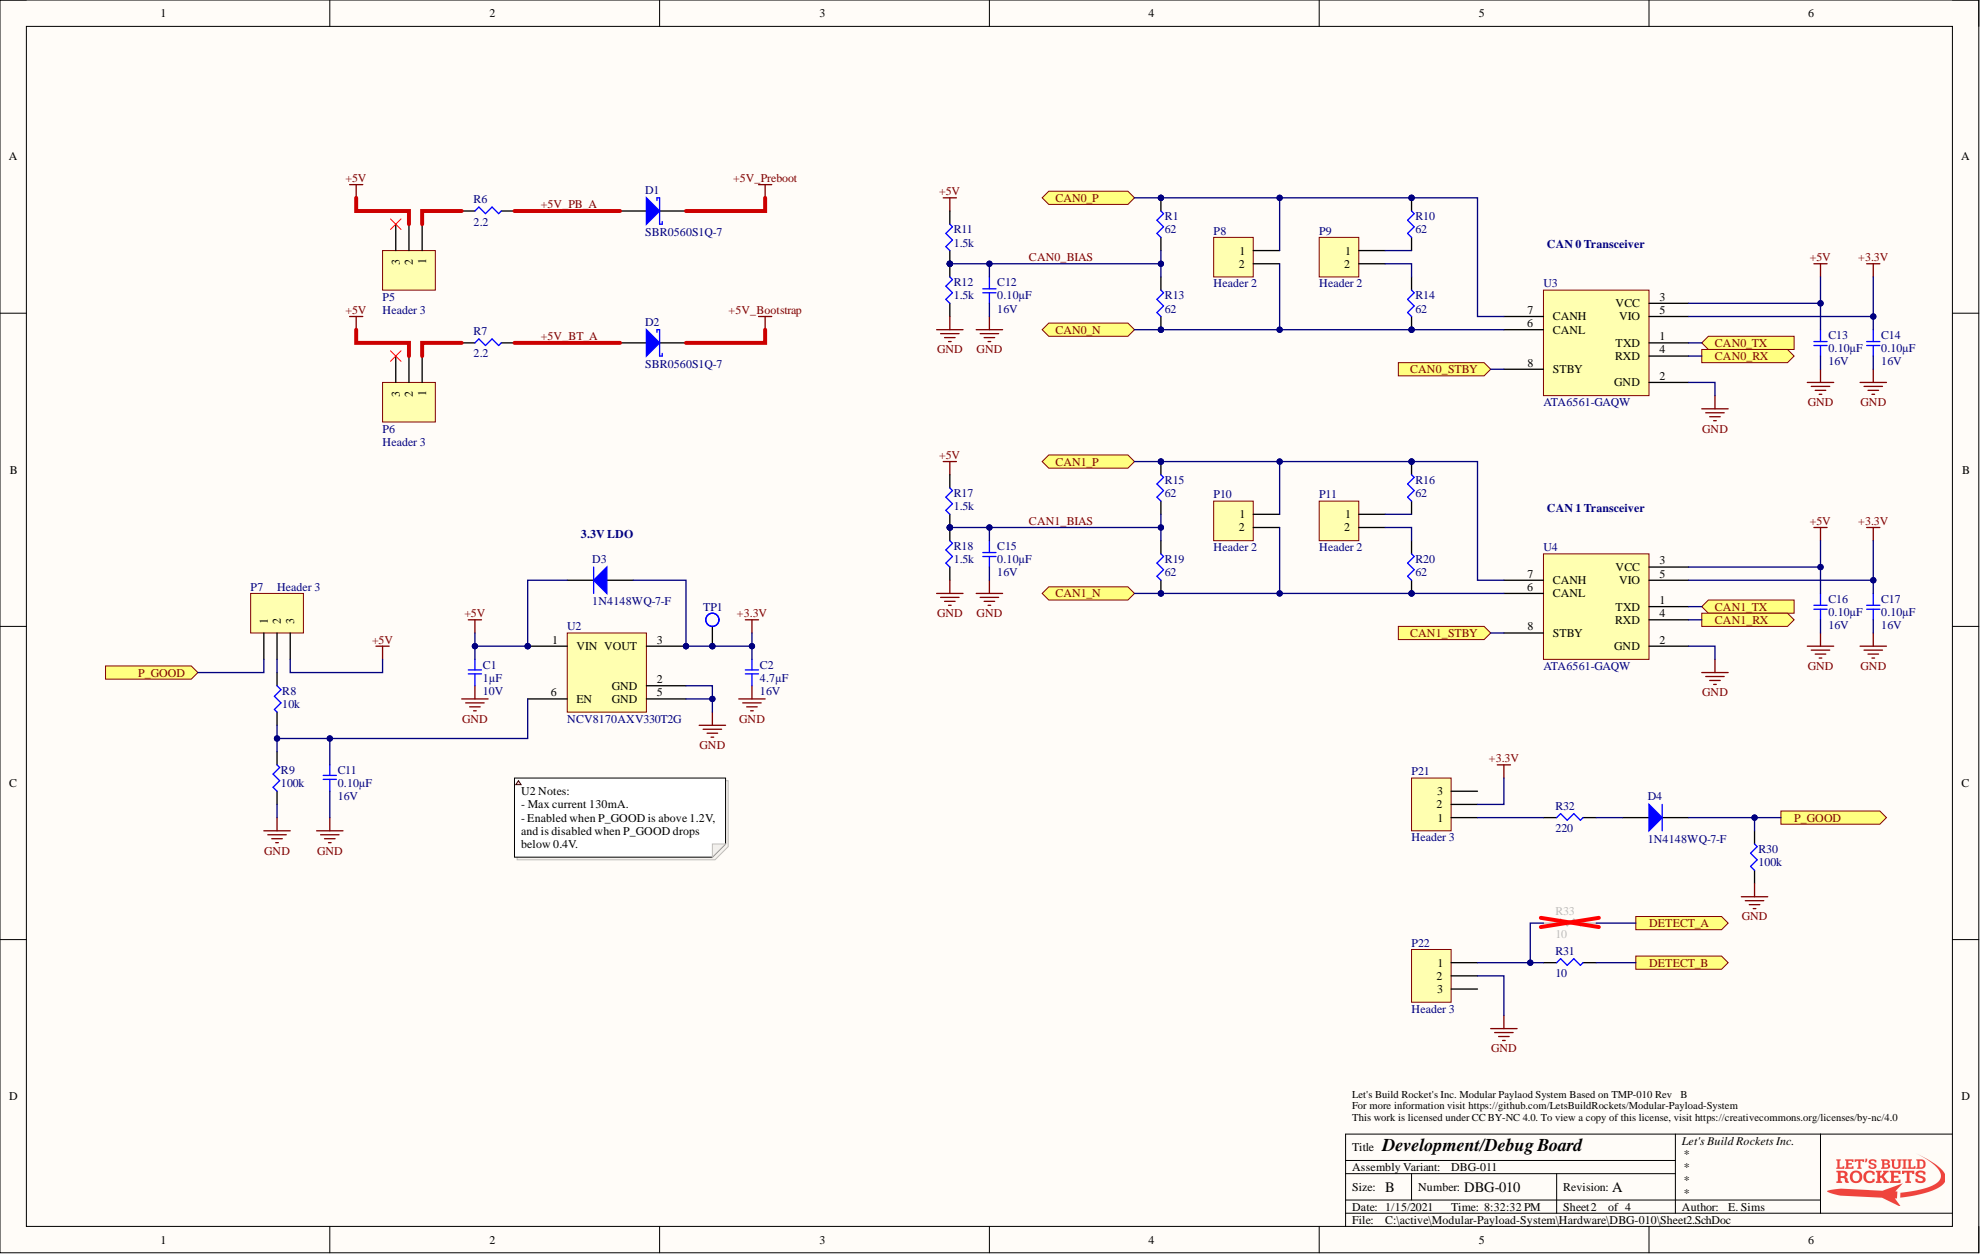
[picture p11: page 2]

ed under CC BY-NC 4.0. To vi

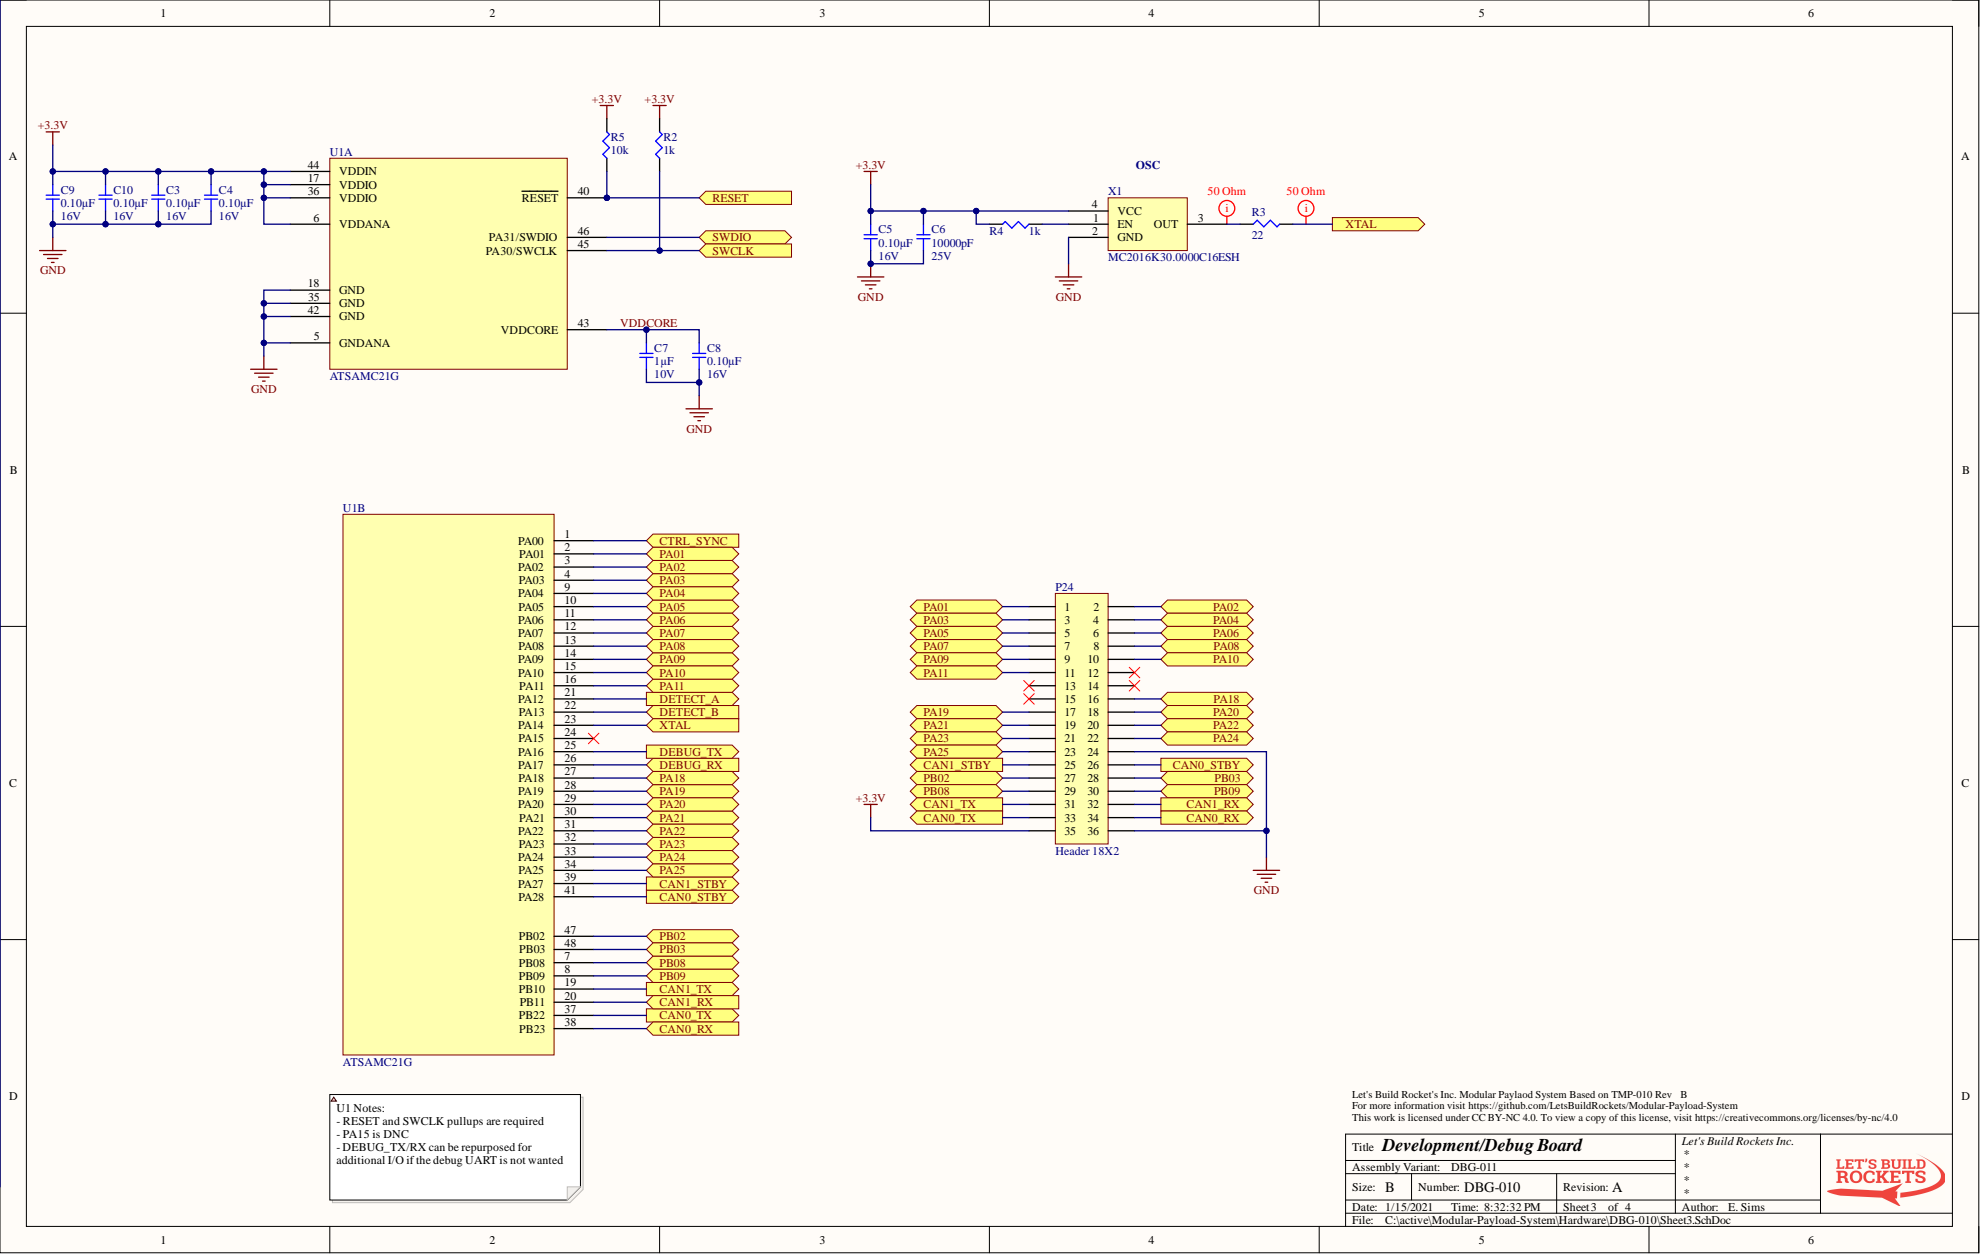
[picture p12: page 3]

VDDIO 36

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

U1 Notes:
- RESET and SWCLK pullups are required
- PA15 is DNC
- DEBUG_TX/RX can be repurposed for
additional I/O if the debug UART is not wanted

Let's Build Rockets Inc.

C:\active\Modular-Payload-System\Hardware\DBG-010\Sheet3.SchDoc

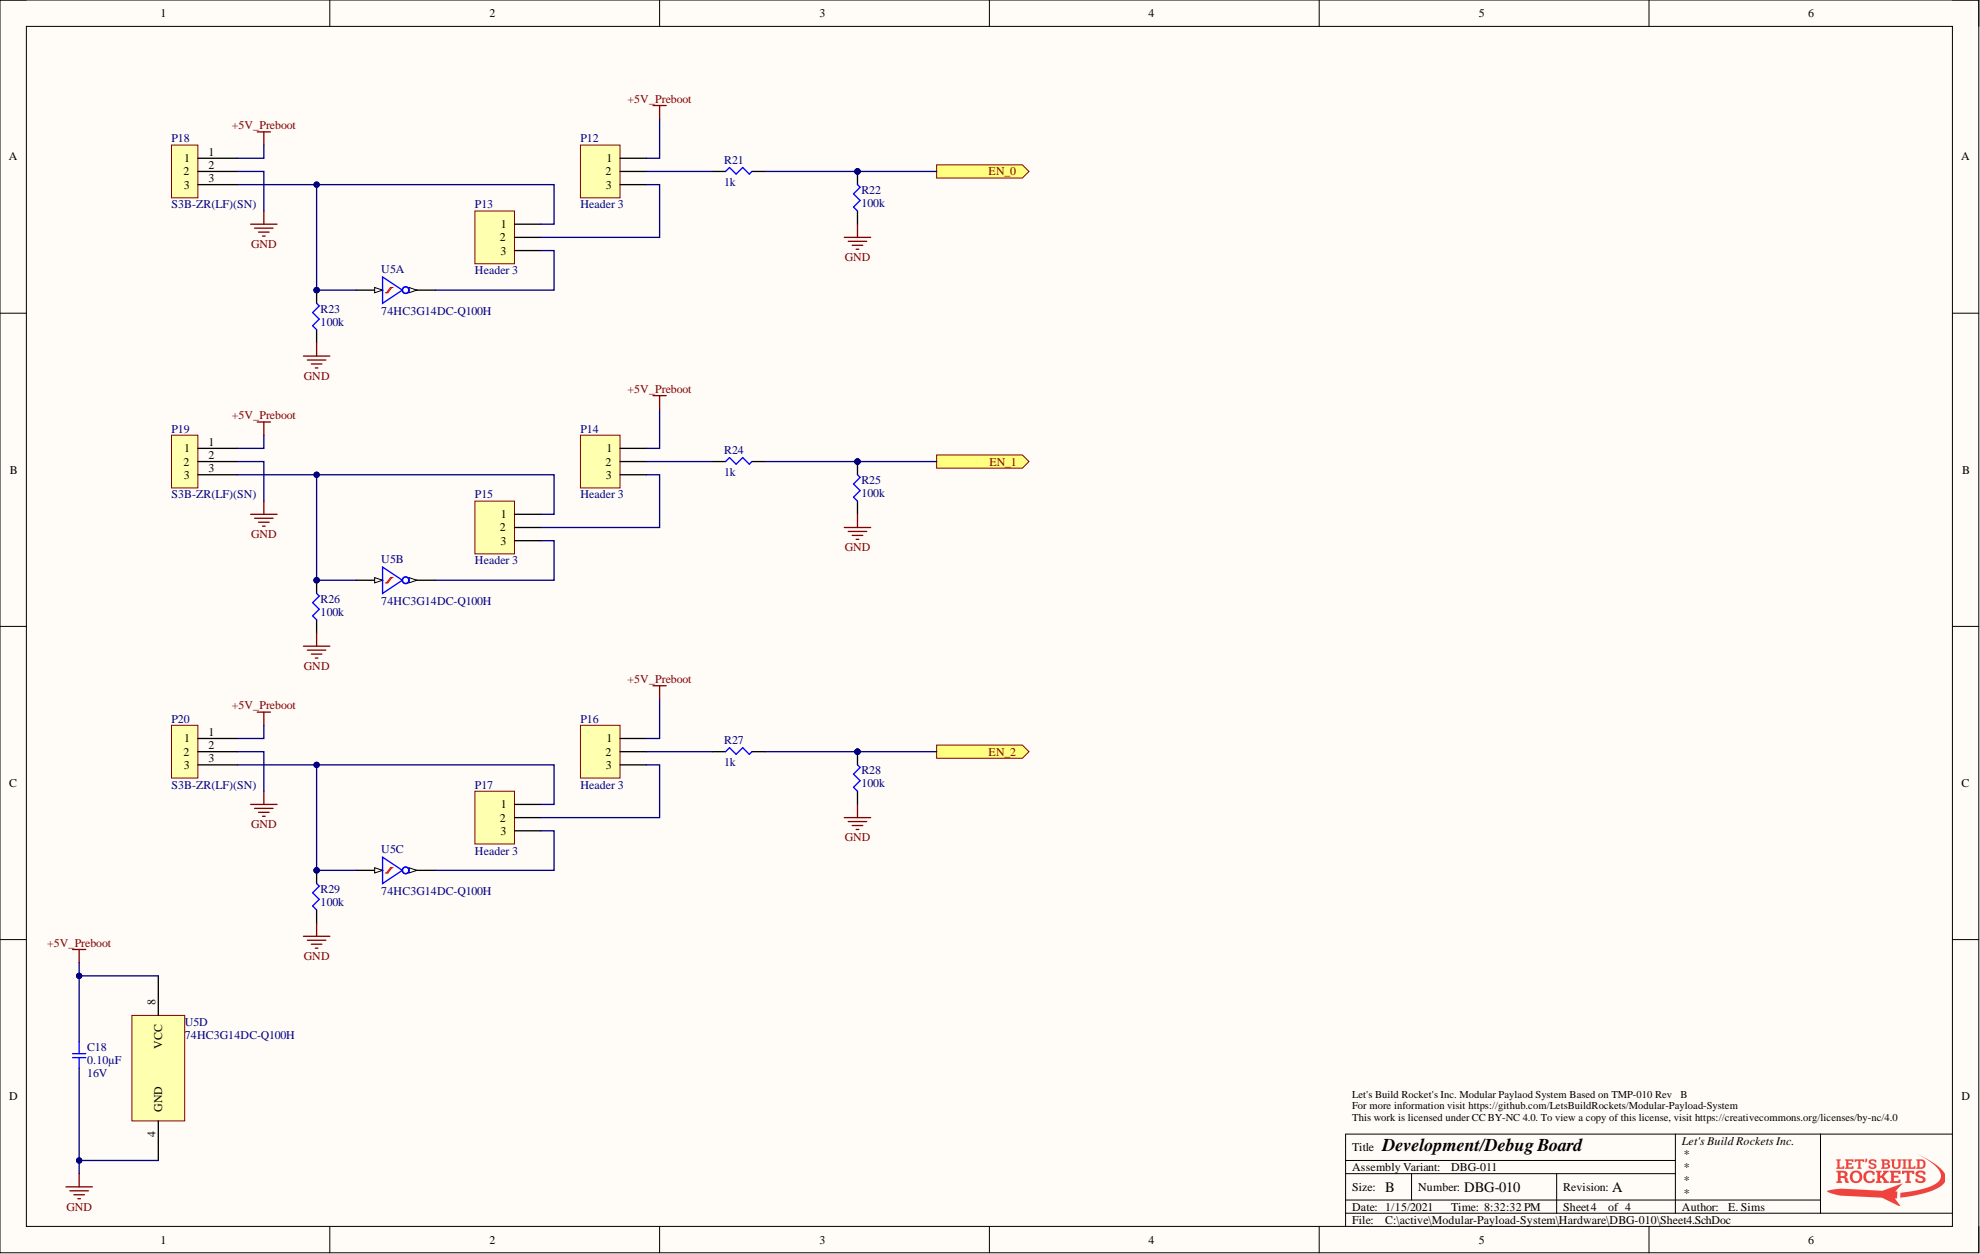
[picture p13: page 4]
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

Let's Build Rockets Inc.

C:\active\Modular-Payload-System\Hardware\DBG-010\Sheet4.SchDoc

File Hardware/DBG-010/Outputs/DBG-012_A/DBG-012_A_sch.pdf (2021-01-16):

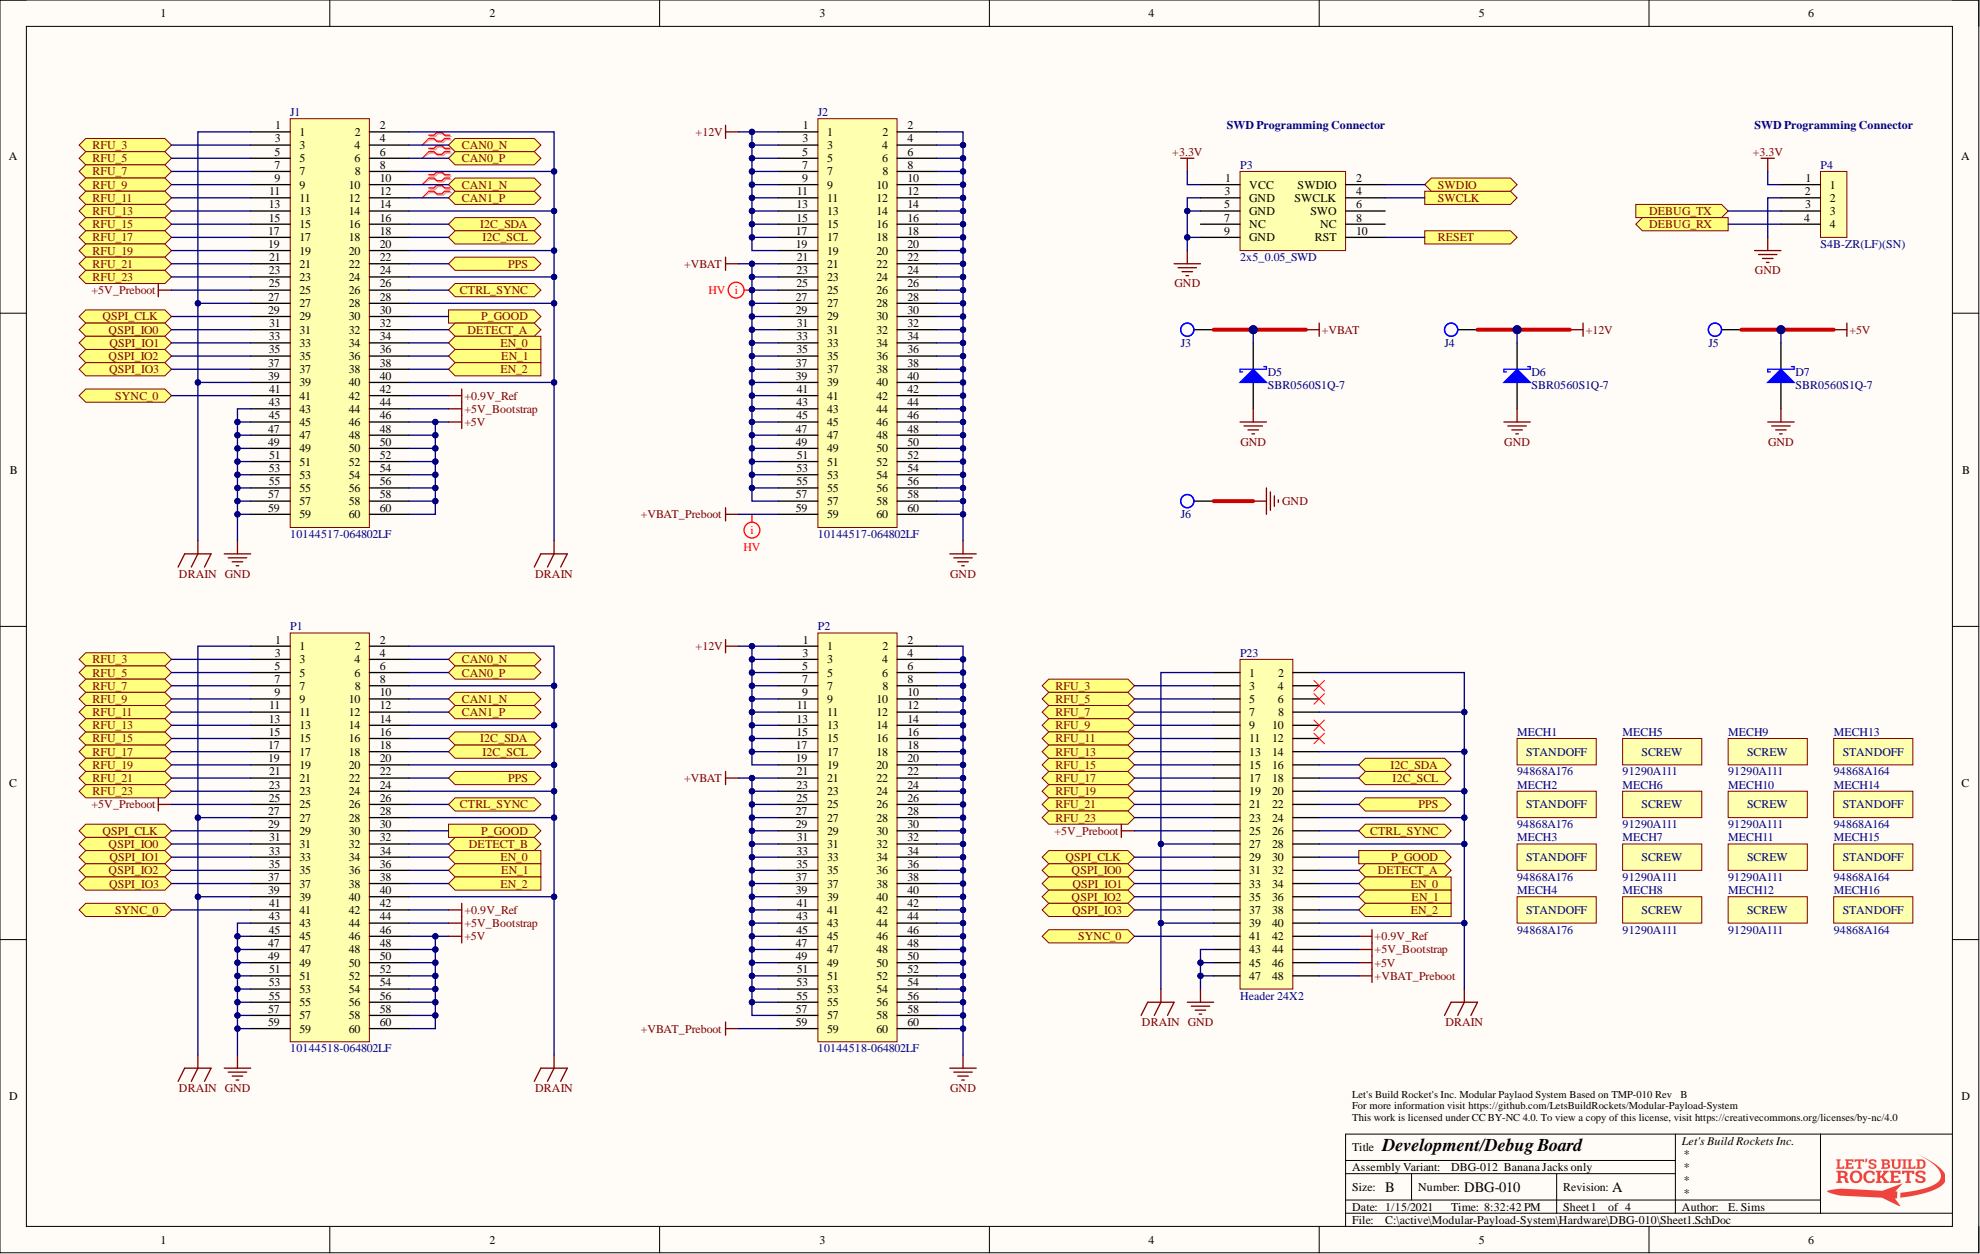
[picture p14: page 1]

Let's Build Rocket's Inc. Modular Paylaod System Based on TMP-010 Rev
For more information visit https://github.com/LetsBuildRockets/Modular-Payload-System
This work is licensed under CC BY-NC 4.0. To view a copy of this license, visit https://creativecommons.org/licenses/by-nc/4.0
Development/Debug Board
Title
Assembly Variant: DBG-012
C:\active\Modular-Payload-System\Hardware\DBG-010\Sheet1.SchDoc

Let's Build Rockets Inc.

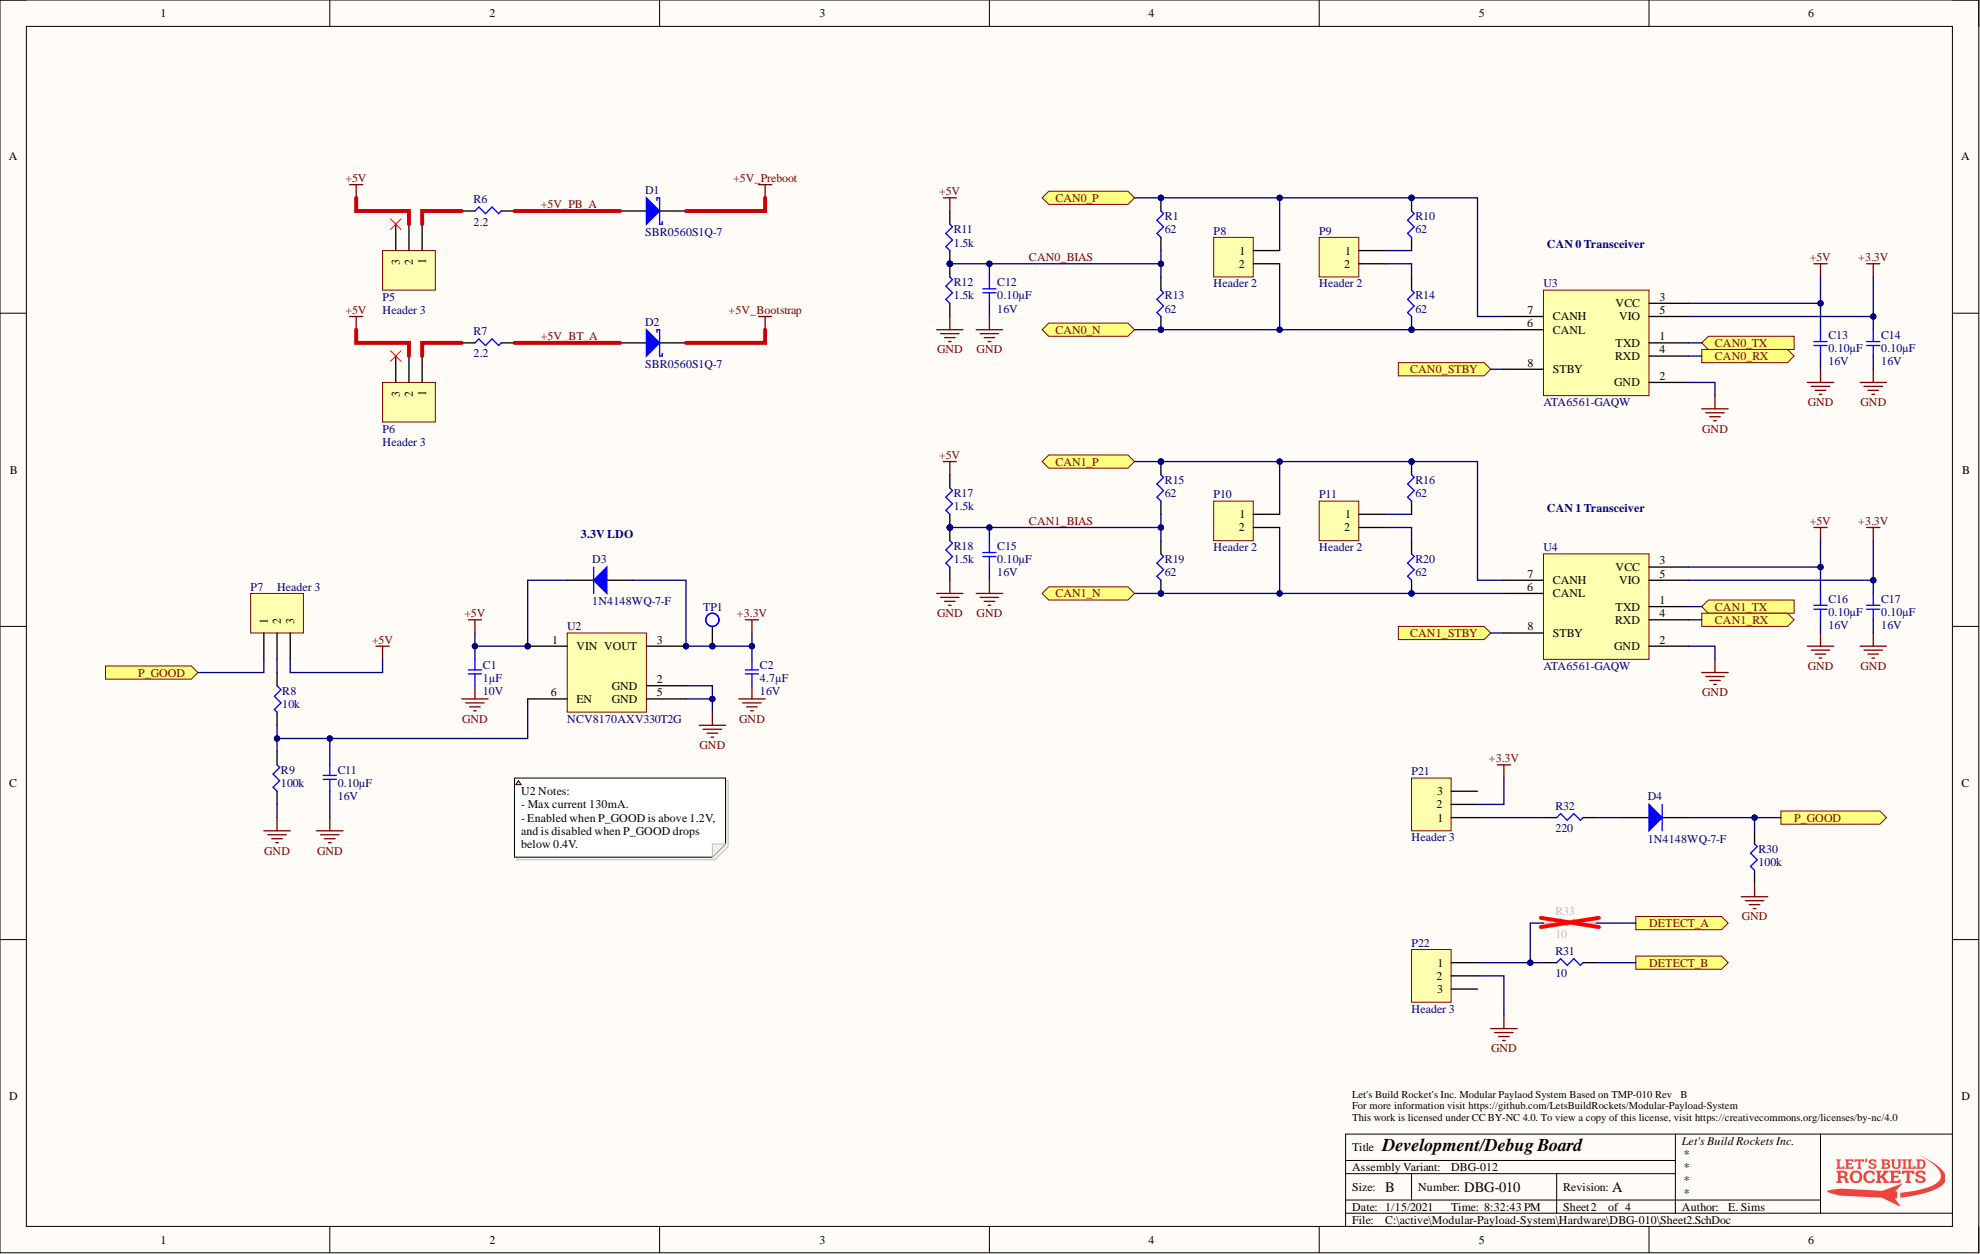
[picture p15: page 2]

ed under CC BY-NC 4.0. To vi

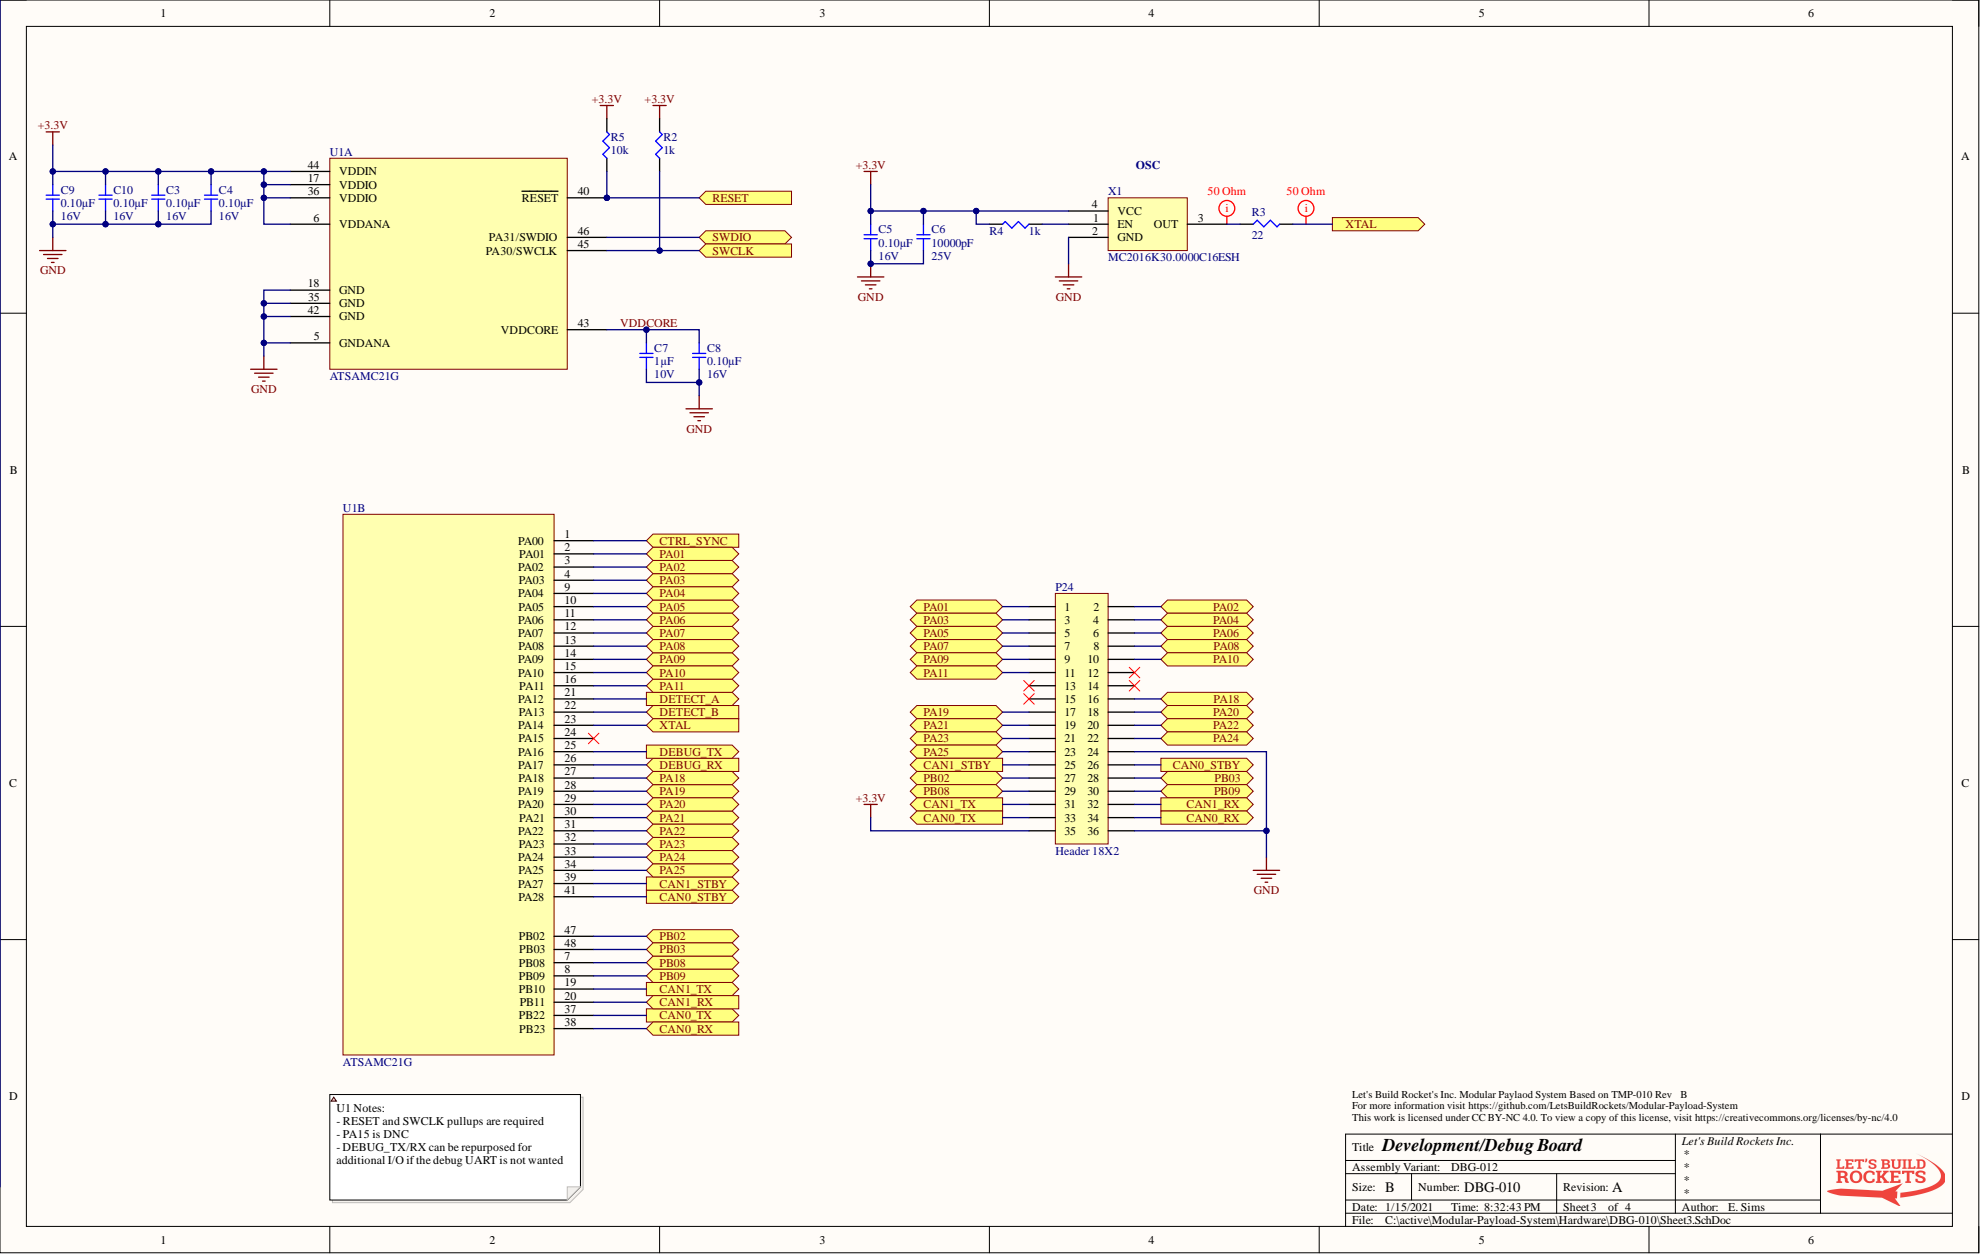
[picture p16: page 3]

VDDIO 36

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

U1 Notes:
- RESET and SWCLK pullups are required
- PA15 is DNC
- DEBUG_TX/RX can be repurposed for
additional I/O if the debug UART is not wanted

Let's Build Rockets Inc.

C:\active\Modular-Payload-System\Hardware\DBG-010\Sheet3.SchDoc

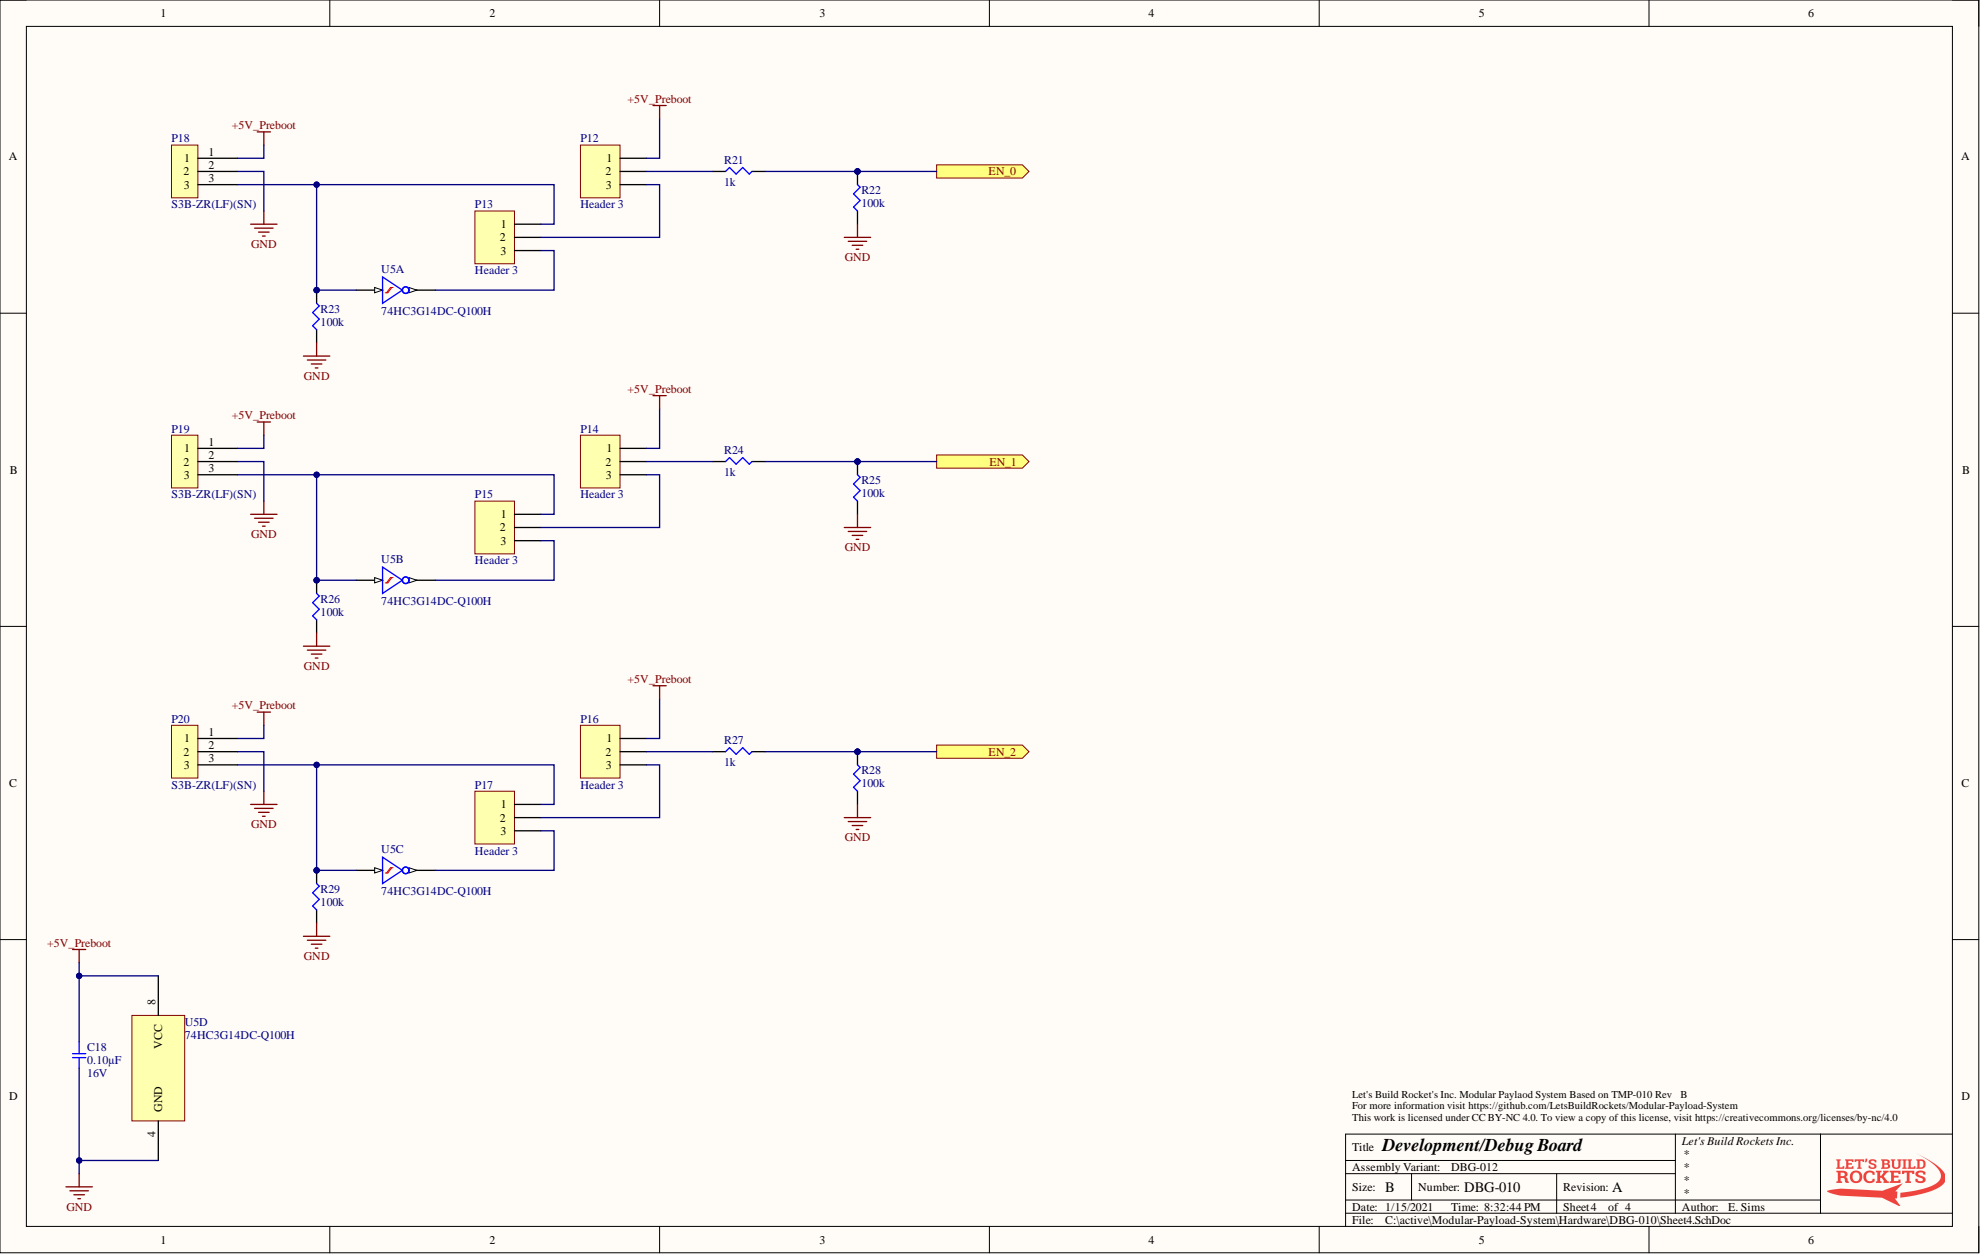
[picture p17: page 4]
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

Let's Build Rockets Inc.

C:\active\Modular-Payload-System\Hardware\DBG-010\Sheet4.SchDoc

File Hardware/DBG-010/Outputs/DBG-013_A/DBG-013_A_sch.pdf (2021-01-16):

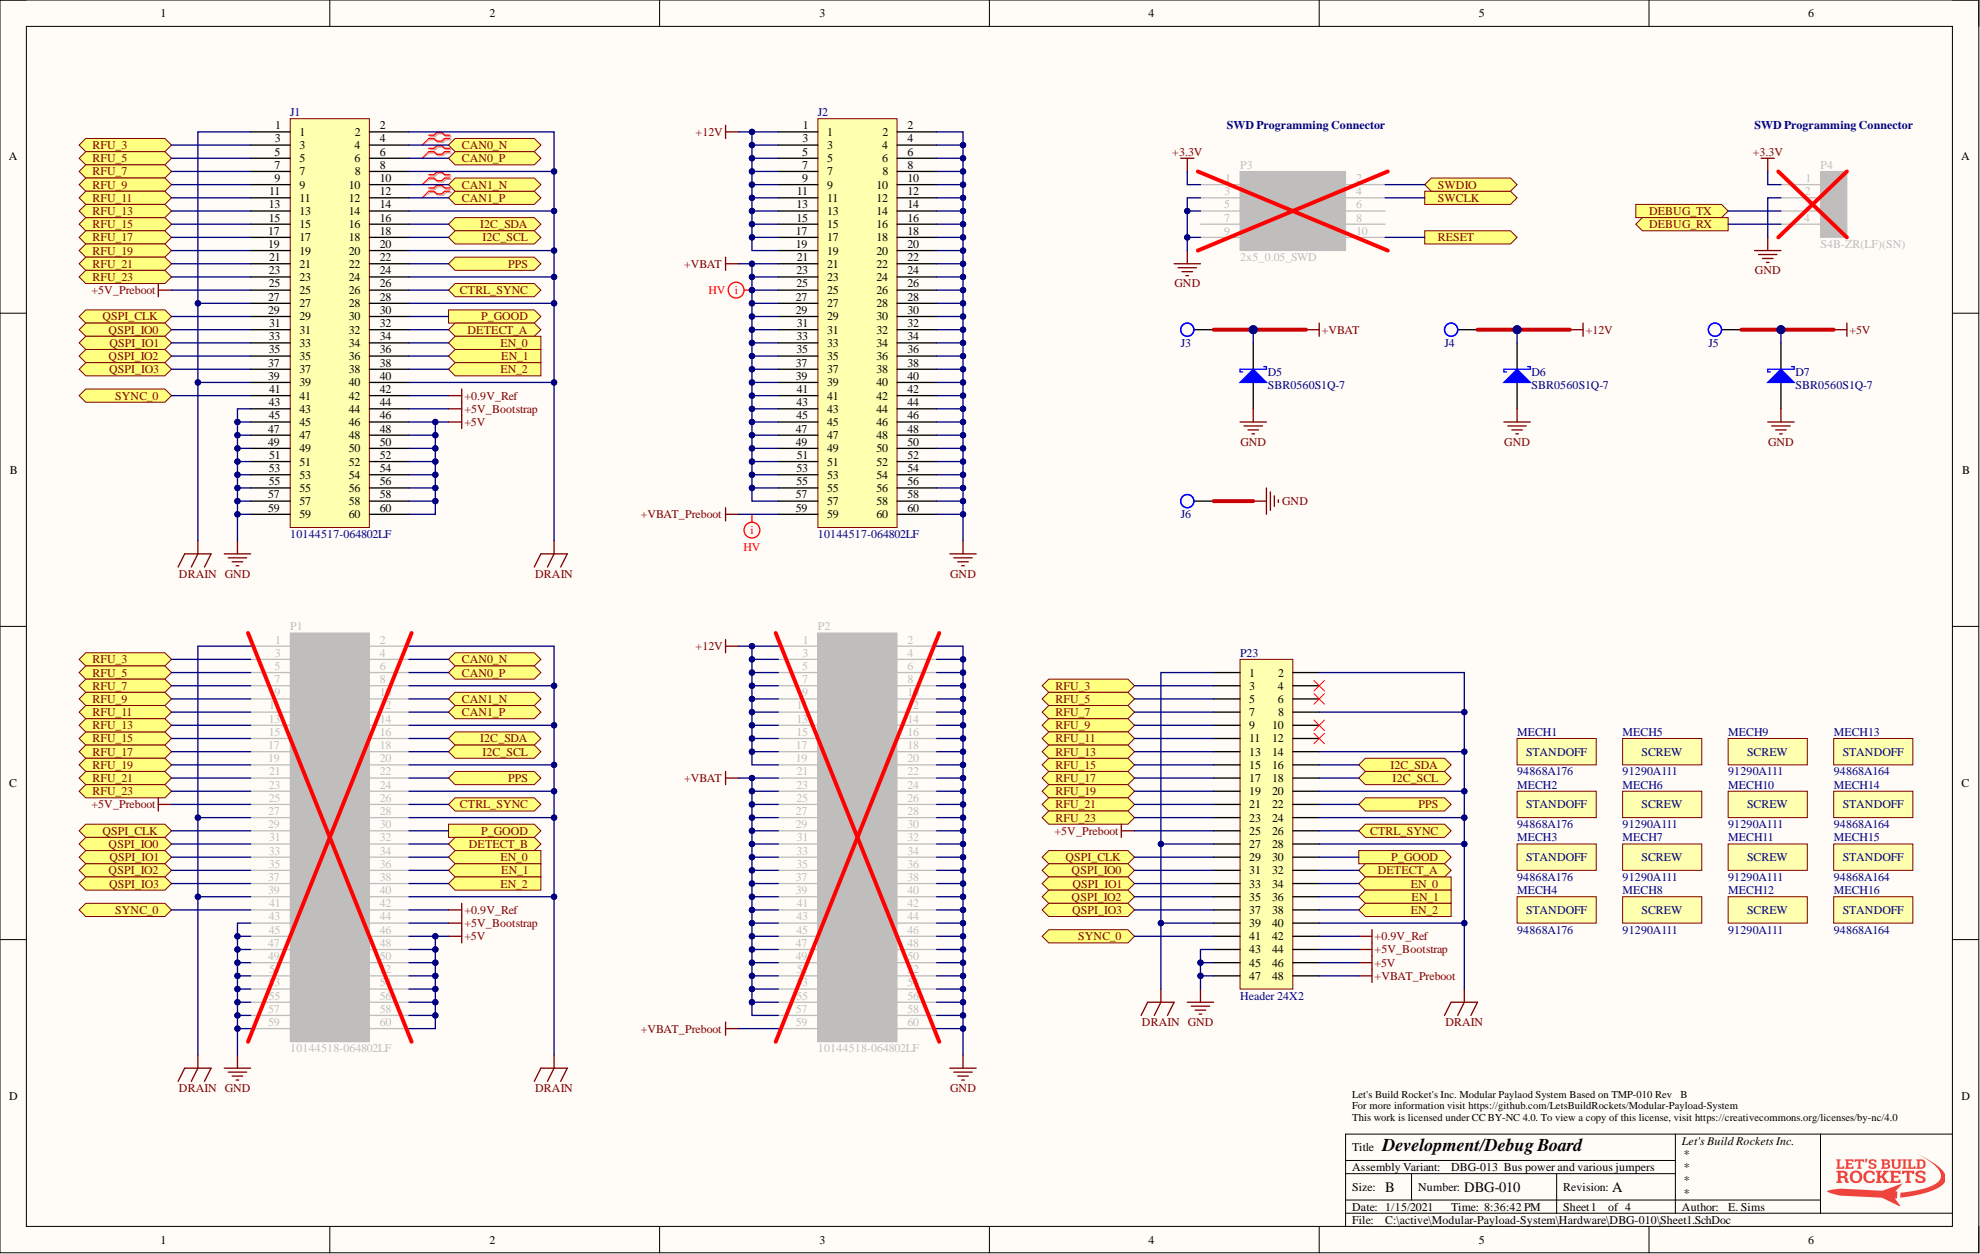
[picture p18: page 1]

Let's Build Rocket's Inc. Modular Paylaod System Based on TMP-010 Rev
For more information visit https://github.com/LetsBuildRockets/Modular-Payload-System
This work is licensed under CC BY-NC 4.0. To view a copy of this license, visit https://creativecommons.org/licenses/by-nc/4.0
Development/Debug Board
Title
Assembly Variant: DBG-013
C:\active\Modular-Payload-System\Hardware\DBG-010\Sheet1.SchDoc

Let's Build Rockets Inc.

Bus power and various jumpers

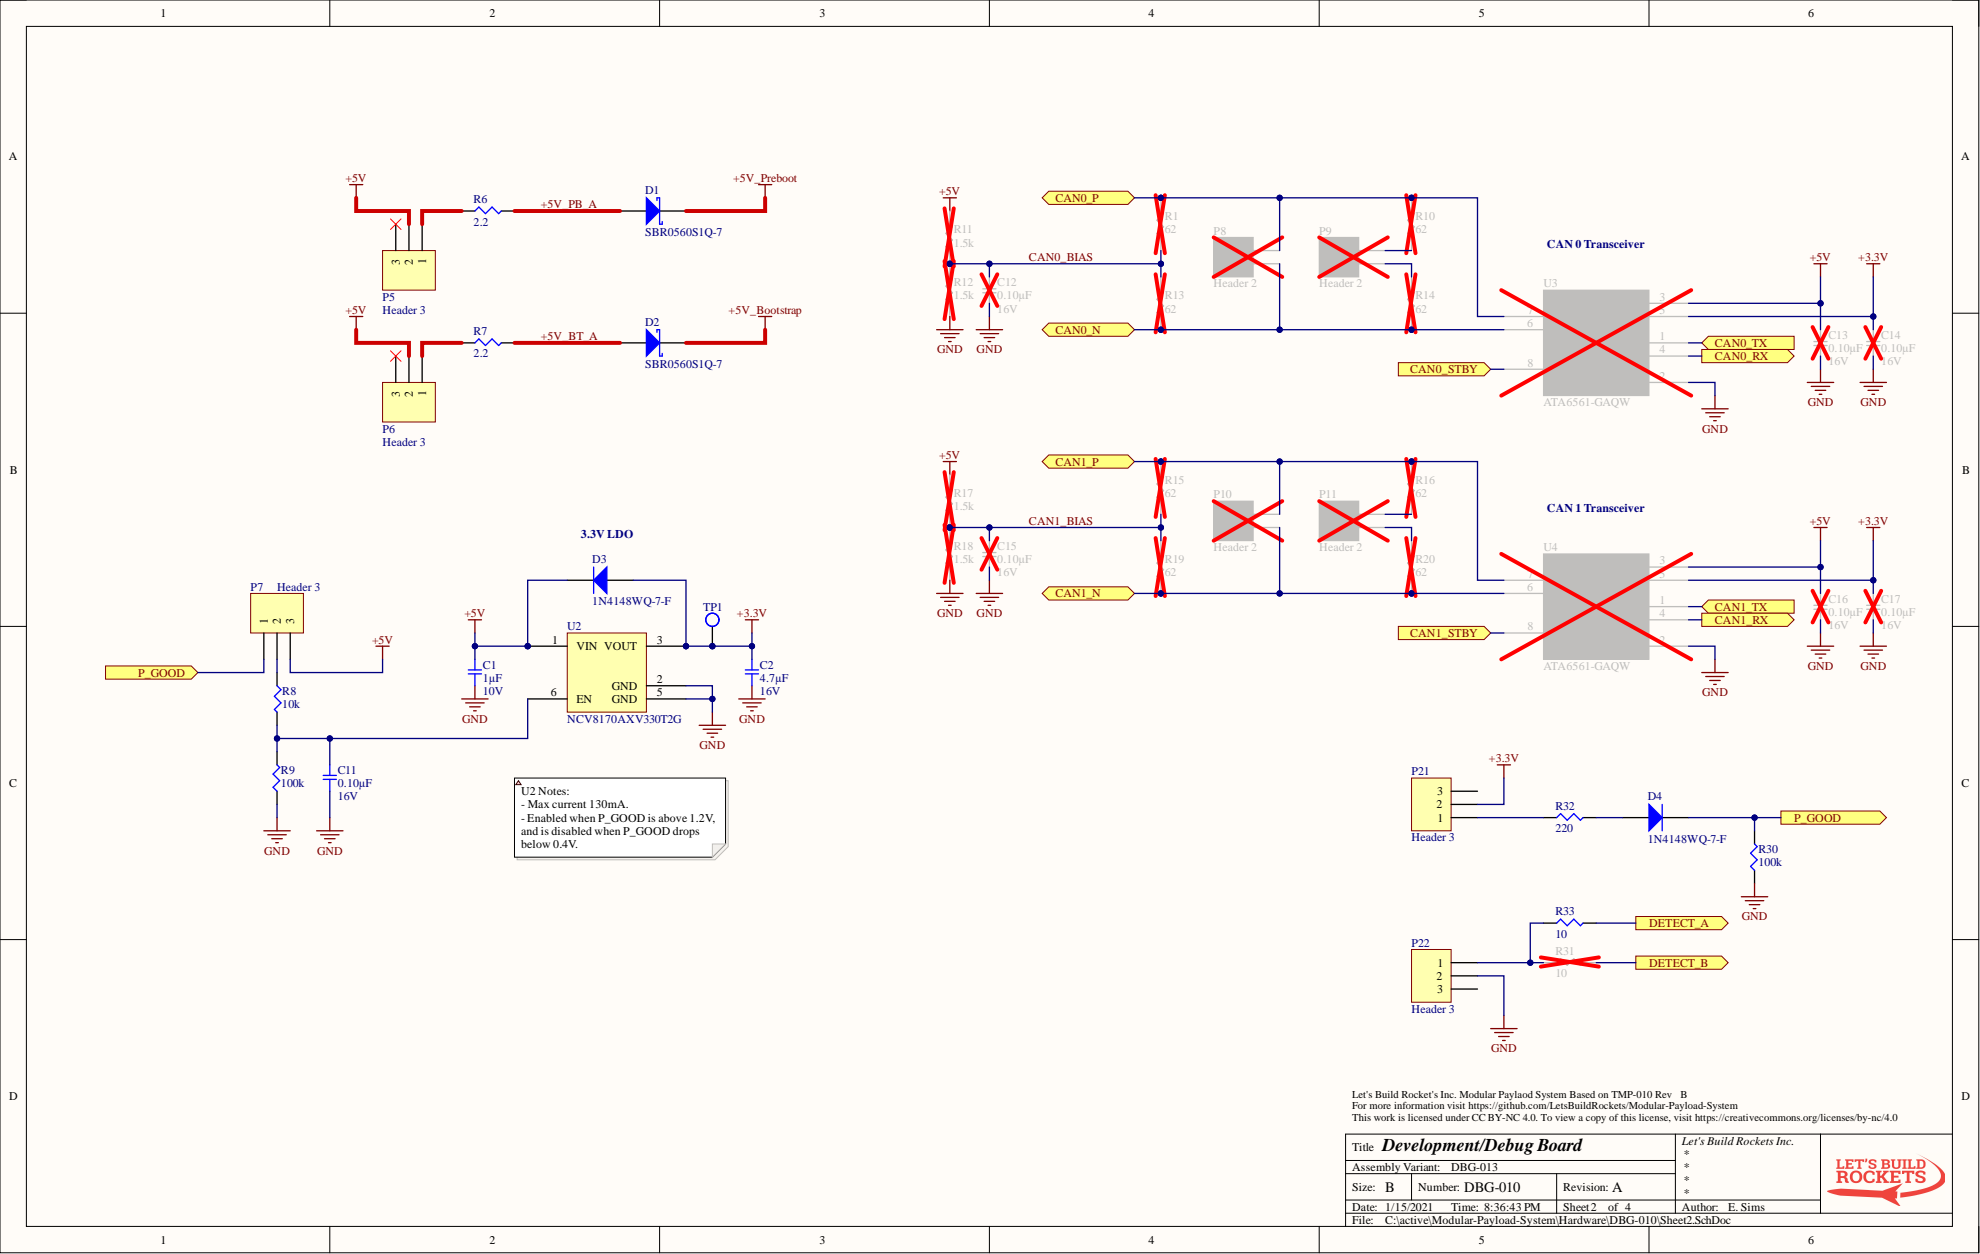
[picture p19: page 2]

ed under CC BY-NC 4.0. To vi

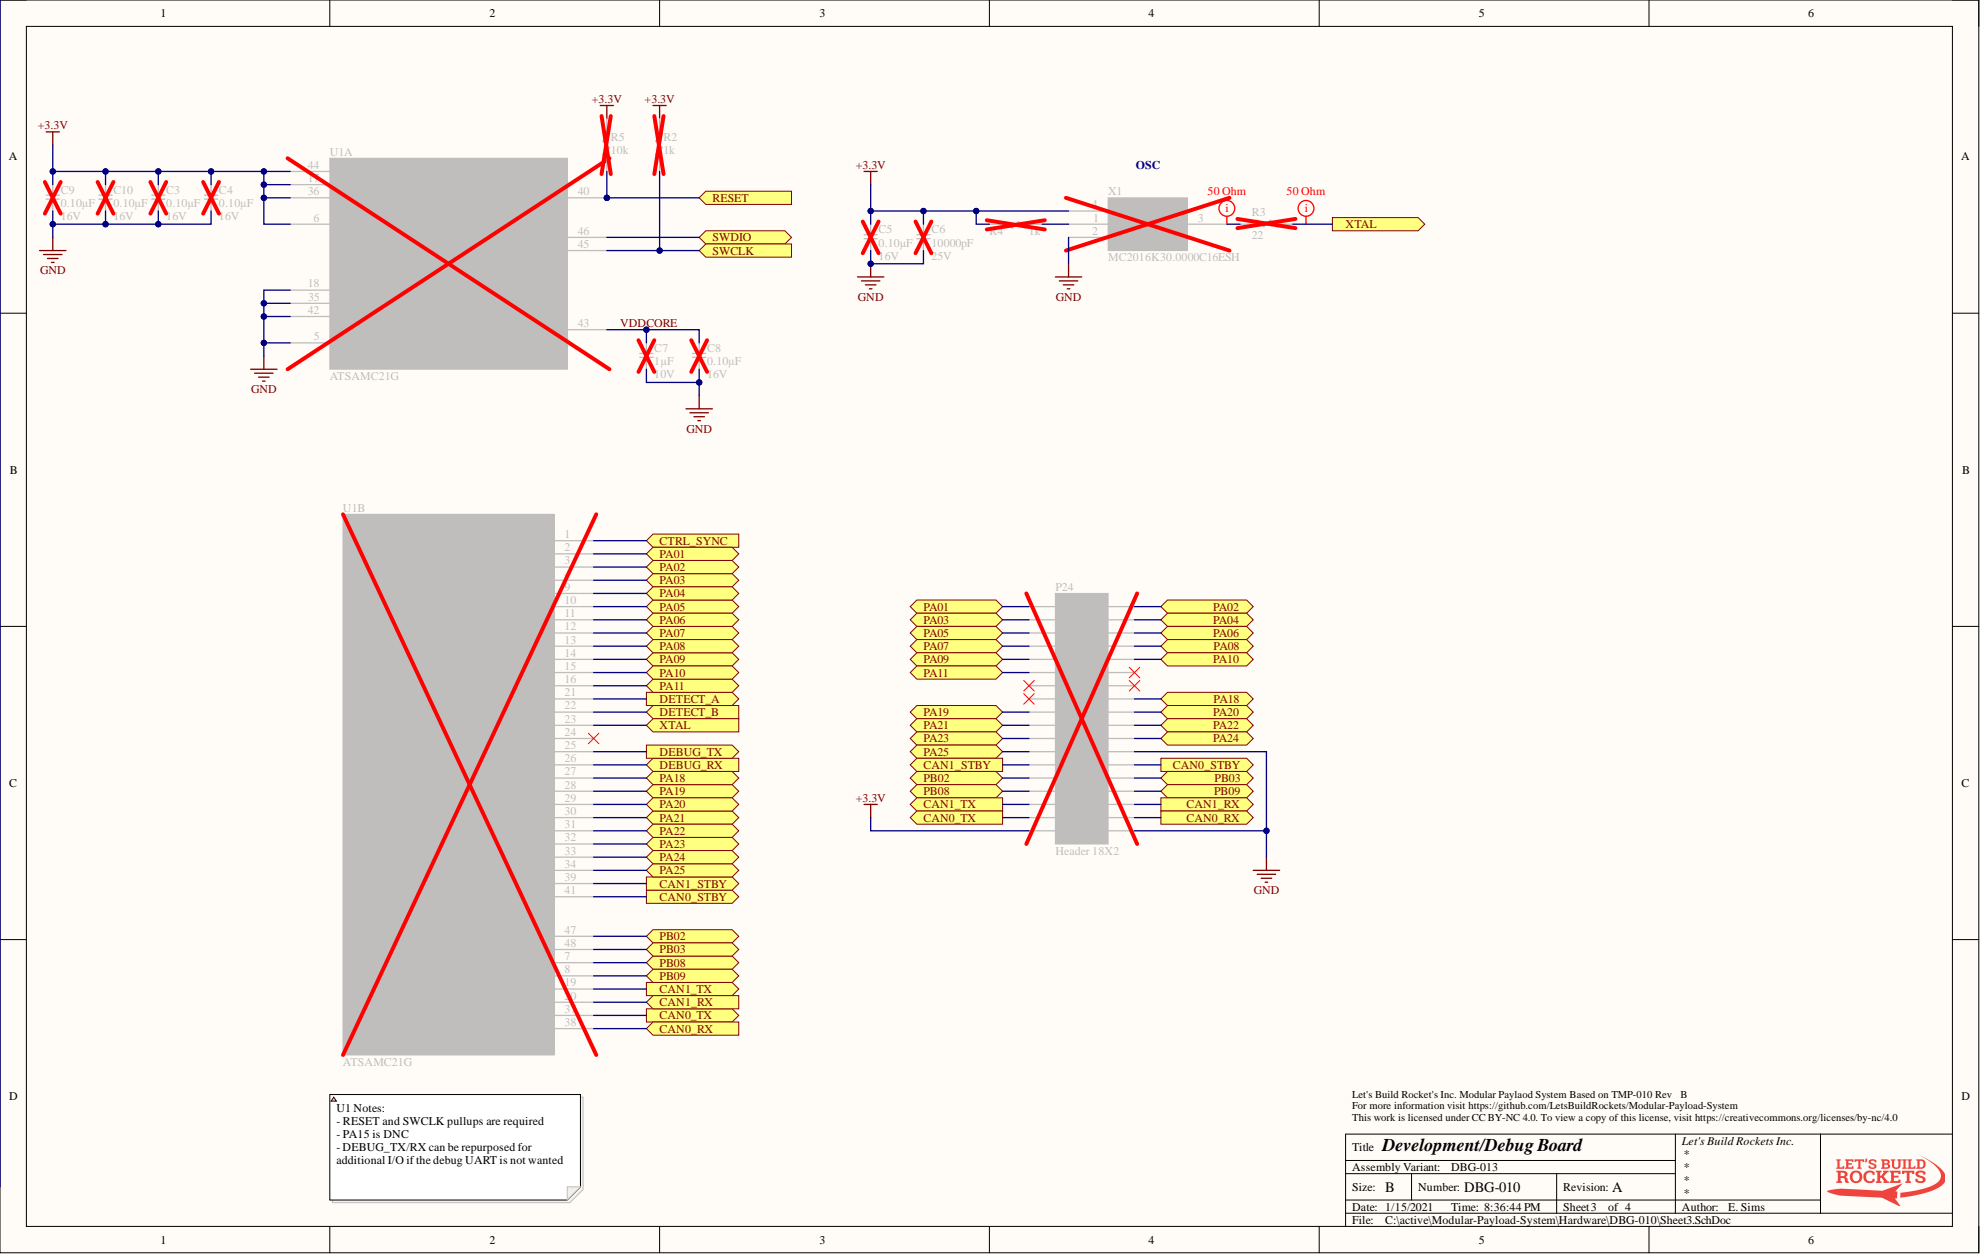
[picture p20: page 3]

VDDIO 36

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

U1 Notes:
- RESET and SWCLK pullups are required
- PA15 is DNC
- DEBUG_TX/RX can be repurposed for
additional I/O if the debug UART is not wanted

Let's Build Rockets Inc.

C:\active\Modular-Payload-System\Hardware\DBG-010\Sheet3.SchDoc

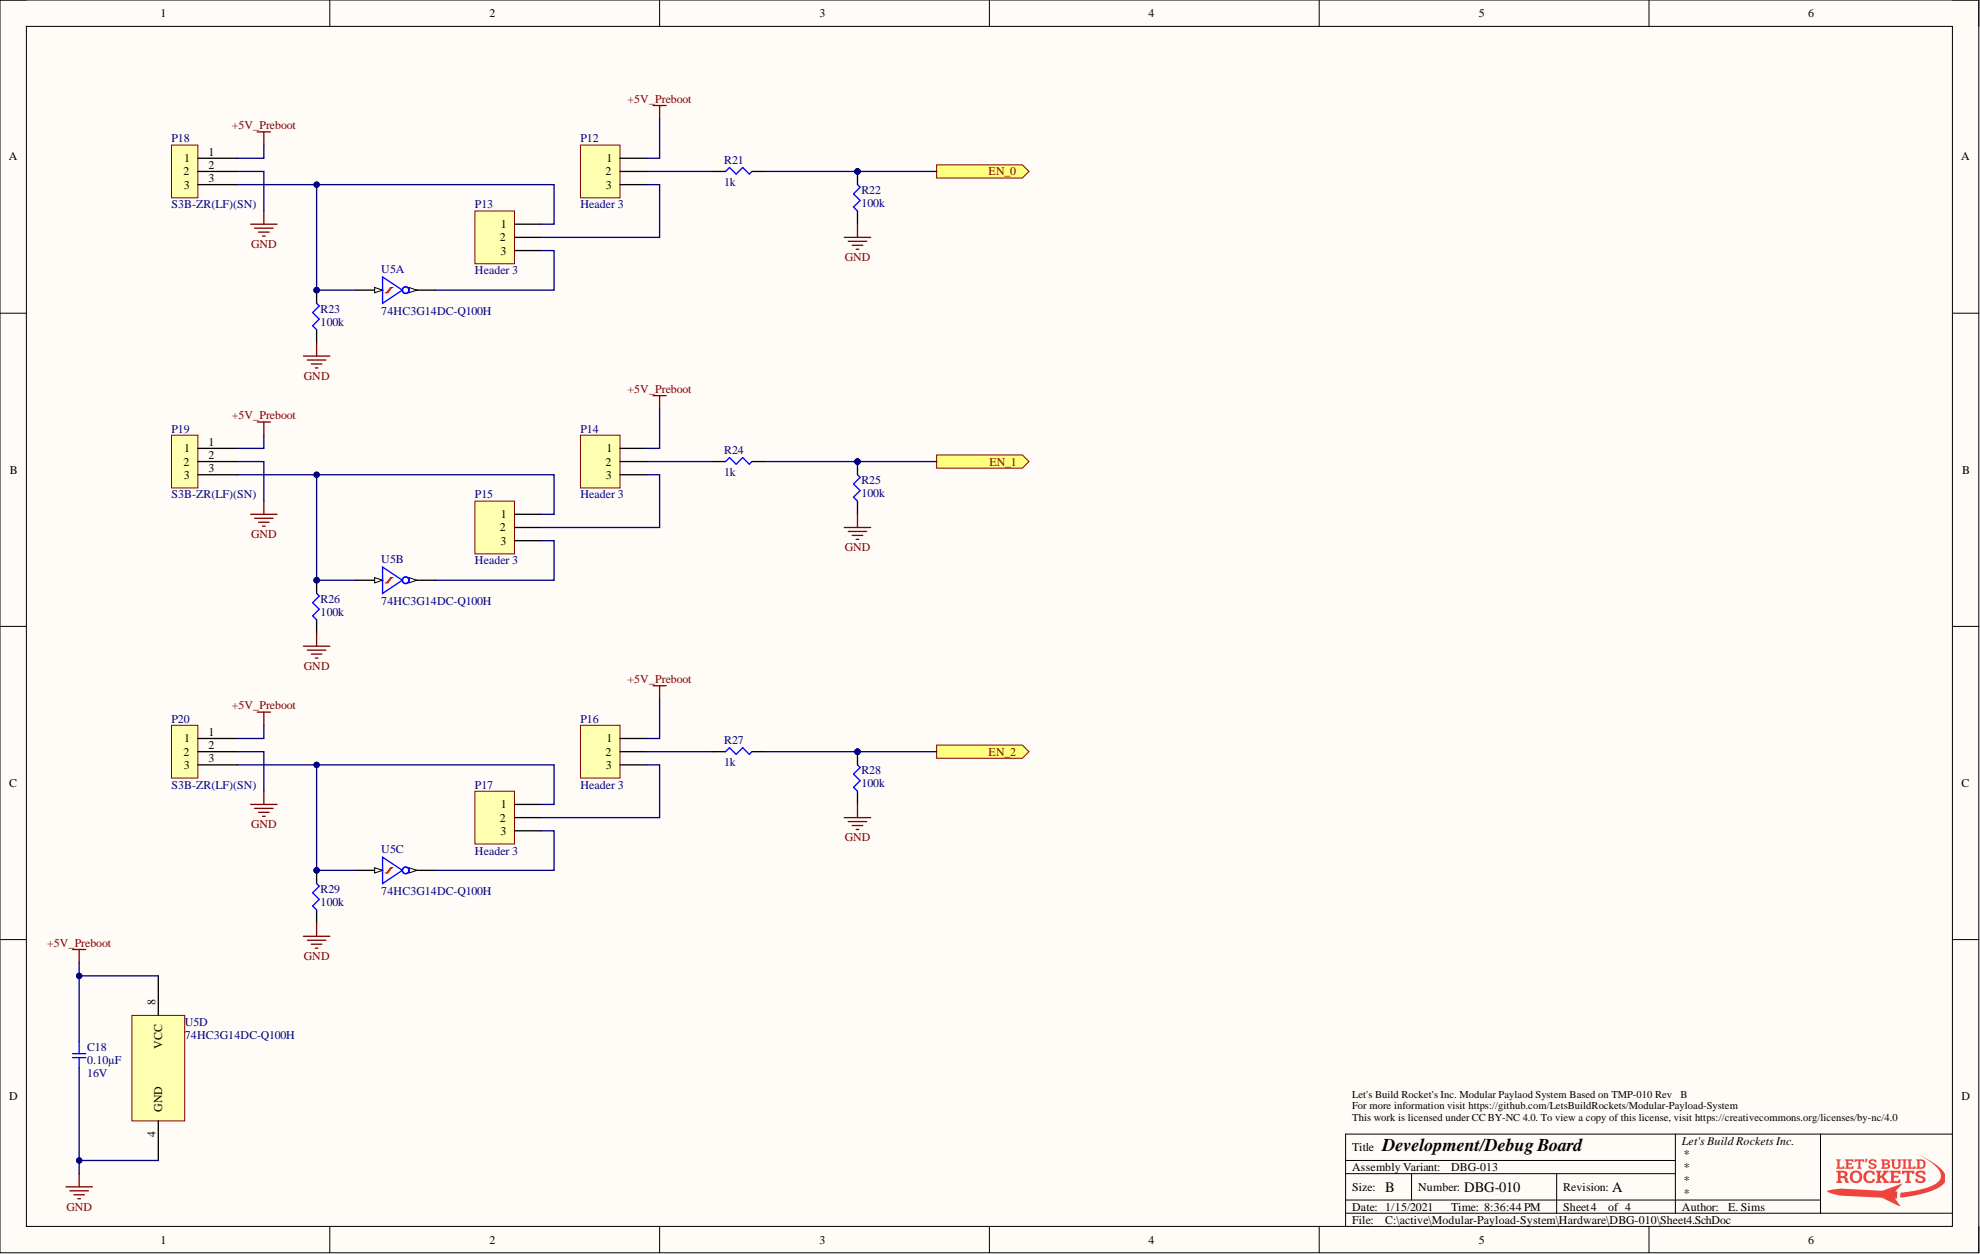
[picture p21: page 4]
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

Let's Build Rockets Inc.

C:\active\Modular-Payload-System\Hardware\DBG-010\Sheet4.SchDoc

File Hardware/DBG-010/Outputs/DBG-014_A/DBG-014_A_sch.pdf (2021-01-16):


Let's Build Rocket's Inc. Modular Paylaod System Based on TMP-010 Rev
For more information visit https://github.com/LetsBuildRockets/Modular-Payload-System
This work is licensed under CC BY-NC 4.0. To view a copy of this license, visit https://creativecommons.org/licenses/by-nc/4.0
Development/Debug Board
Title
Assembly Variant: DBG-014
C:\active\Modular-Payload-System\Hardware\DBG-010\Sheet1.SchDoc

Let's Build Rockets Inc.

Bus power and various jumpers


ed under CC BY-NC 4.0. To vi


VDDIO 36

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

U1 Notes:
- RESET and SWCLK pullups are required
- PA15 is DNC
- DEBUG_TX/RX can be repurposed for
additional I/O if the debug UART is not wanted

Let's Build Rockets Inc.

C:\active\Modular-Payload-System\Hardware\DBG-010\Sheet3.SchDoc

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

Let's Build Rockets Inc.

C:\active\Modular-Payload-System\Hardware\DBG-010\Sheet4.SchDoc

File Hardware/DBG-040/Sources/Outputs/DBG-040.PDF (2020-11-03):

+5V +5V_Boot; RFU_15 RFU_17 RFU_19 RFU_21 RFU_23 RFU_25; RFU_3 RFU_5 RFU_7 RFU_9 RFU_1; RFU_13 RFU_15 RFU_17 RFU_19 RFU_21 RFU_23 RFU_25 QSPI_C; ld Rocket; s Inc. Modular Paylaod Sys; tem Based on T MP-001 Rev; ion vi; s work i; icensed under C C B; icense, vi

5 PIJ205 PIJ205 | 6 PIJ206 PIJ206
PIJ207 | 7 | 8 PIJ208 PIJ208

PIJ405 | 5 | PIJ406 PIJ406 6
PIJ407 | 7 | 8 PIJ408 PIJ408

s Bui
Let
For more infor
Thi

t https
C 4.0. To view a copy of thi

Ti t l e Sp acer B o ard | Let 's Bui ld Rockets Inc. *** *

Size: B | Number : D B G -0 4 0 | Revi s ion: A . 1
Date: 11/2/2020 Ti me: 9:50:18 PM | | Sheet 1 of 1
Fi le: Sheet1.SchDoc



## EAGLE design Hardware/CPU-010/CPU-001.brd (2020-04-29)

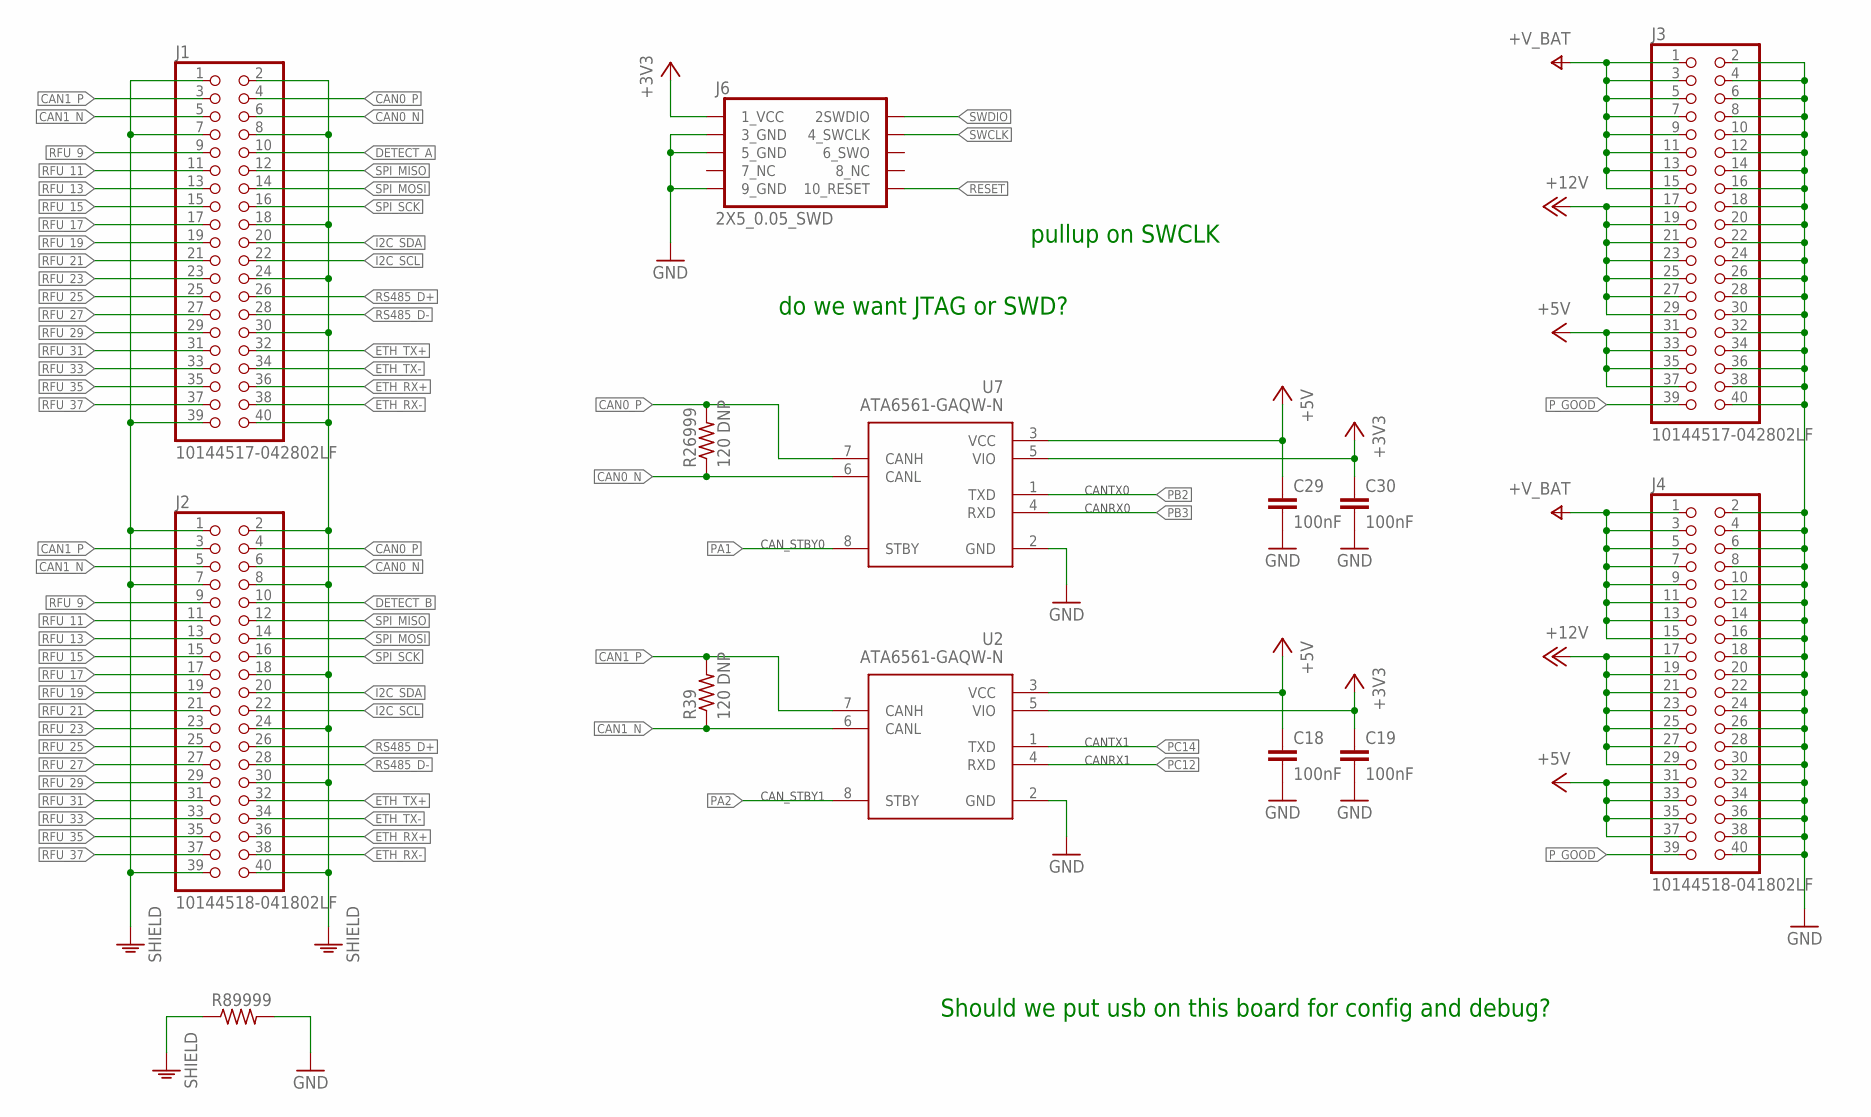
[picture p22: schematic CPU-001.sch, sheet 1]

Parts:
C18, C19, C29, C30: 100nF; C0402
J1, J3: 10144517-042802LF
J2, J4: 10144518-041802LF
J6: 2X5_0.05_SWD; 2X5_RIGHT
R39, R26999: 120 DNP; R0402
R89999: R-US_R0402; R0402
U2, U7: ATA6561-GAQW-N; SOIC127P600X175-8N

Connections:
+3V3: C19.1, C30.1, J6.1 (1_VCC), U2.5 (VIO), U7.5 (VIO); also elsewhere on the board
+5V: C18.1, C29.1, J3.31, J3.33, J3.35, J3.37, J4.31, J4.33, J4.35, J4.37, U2.3 (VCC), U7.3 (VCC); also elsewhere on the board
+12V: J3.17, J3.19, J3.21, J3.23, J3.25, J3.27, J3.29, J4.17, J4.19, J4.21, J4.23, J4.25, J4.27, J4.29
+V_BAT: J3.1, J3.3, J3.5, J3.7, J3.9, J3.11, J3.13, J3.15, J4.1, J4.3, J4.5, J4.7, J4.9, J4.11, J4.13, J4.15
CAN0_N: J1.6, J2.6, R26999.1, U7.6 (CANL)
CAN0_P: J1.4, J2.4, R26999.2, U7.7 (CANH)
CAN1_N: J1.5, J2.5, R39.1, U2.6 (CANL)
CAN1_P: J1.3, J2.3, R39.2, U2.7 (CANH)
DETECT_A: J1.10
DETECT_B: J2.10
ETH_RX+: J1.36, J2.36
ETH_RX-: J1.38, J2.38
ETH_TX+: J1.32, J2.32
ETH_TX-: J1.34, J2.34
GND: C18.2, C19.2, C29.2, C30.2, J3.2, J3.4, J3.6, J3.8, J3.10, J3.12, J3.14, J3.16, J3.18, J3.20, J3.22, J3.24, J3.26, J3.28, J3.30, J3.32, J3.34, J3.36, J3.38, J3.40, J4.2, J4.4, J4.6, J4.8, J4.10, J4.12, J4.14, J4.16, J4.18, J4.20, J4.22, J4.24, J4.26, J4.28, J4.30, J4.32, J4.34, J4.36, J4.38, J4.40, J6.3 (3_GND), J6.5 (5_GND), J6.9 (9_GND), R89999.2, U2.2 (GND), U7.2 (GND); also elsewhere on the board
I2C_SCL: J1.22, J2.22
I2C_SDA: J1.20, J2.20
PA1: U7.8 (STBY); also elsewhere on the board
PA2: U2.8 (STBY); also elsewhere on the board
PB2: U7.1 (TXD); also elsewhere on the board
PB3: U7.4 (RXD); also elsewhere on the board
PC12: U2.4 (RXD); also elsewhere on the board
PC14: U2.1 (TXD); also elsewhere on the board
P_GOOD: J3.39, J4.39
RESET: J6.10 (10_RESET)
RFU_9: J1.9, J2.9
RFU_11: J1.11, J2.11
RFU_13: J1.13, J2.13
RFU_15: J1.15, J2.15
RFU_17: J1.17, J2.17
RFU_19: J1.19, J2.19
RFU_21: J1.21, J2.21
RFU_23: J1.23, J2.23
RFU_25: J1.25, J2.25
RFU_27: J1.27, J2.27
RFU_29: J1.29, J2.29
RFU_31: J1.31, J2.31
RFU_33: J1.33, J2.33
RFU_35: J1.35, J2.35
RFU_37: J1.37, J2.37
RS485_D+: J1.26, J2.26
RS485_D-: J1.28, J2.28
SHIELD: J1.1, J1.2, J1.7, J1.8, J1.18, J1.24, J1.30, J1.39, J1.40, J2.1, J2.2, J2.7, J2.8, J2.18, J2.24, J2.30, J2.39, J2.40, R89999.1
SPI_MISO: J1.12, J2.12
SPI_MOSI: J1.14, J2.14
SPI_SCK: J1.16, J2.16
SWCLK: J6.4 (4_SWCLK)
SWDIO: J6.2 (2SWDIO)

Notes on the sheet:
do we want JTAG or SWD?
Should we put usb on this board for config and debug?
pullup on SWCLK
CAN_STBY0
CAN_STBY1
CANTX0
CANRX0
CANRX1
CANTX1

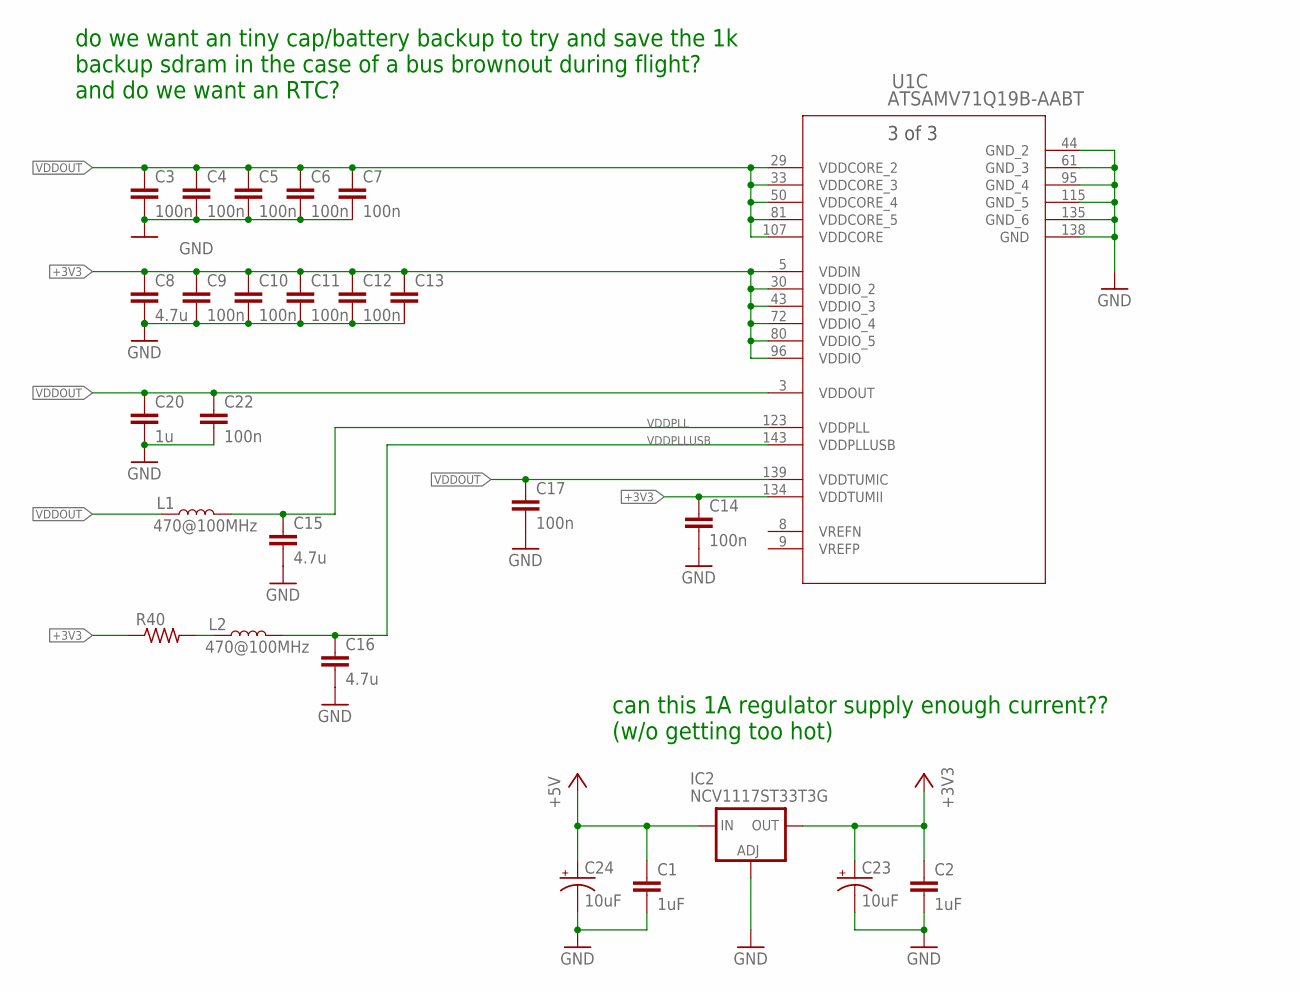
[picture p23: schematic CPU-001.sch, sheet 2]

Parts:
C1, C2: 1uF; C0603
C3, C4, C5, C6, C7, C9, C10, C11, C12, C13, C14, C17, C22: 100n; C0402
C8, C15, C16: 4.7u; C0805
C20: 1u; C0402
C23, C24: 10uF; 0603-POLAR
IC2: NCV1117ST33T3G; SOT223
L1, L2: 470@100MHz; 0603
R40: R-US_R0402; R0402
U1: ATSAMV71Q19B-AABT; LQFP144_20X20MC

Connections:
+3V3: C2.1, C8.1, C9.1, C10.1, C11.1, C12.1, C13.1, C14.1, C23.+, IC2.4 (OUT), R40.1, U1.5 (VDDIN), U1.30 (VDDIO_2), U1.43 (VDDIO_3), U1.72 (VDDIO_4), U1.80 (VDDIO_5), U1.96 (VDDIO), U1.134 (VDDTUMII); also elsewhere on the board
+5V: C1.1, C24.+, IC2.3 (IN); also elsewhere on the board
GND: C1.2, C2.2, C3.2, C4.2, C5.2, C6.2, C7.2, C8.2, C9.2, C10.2, C11.2, C12.2, C13.2, C14.2, C15.2, C16.2, C17.2, C20.2, C22.2, C23.-, C24.-, IC2.1 (ADJ), U1.44 (GND_2), U1.61 (GND_3), U1.95 (GND_4), U1.115 (GND_5), U1.135 (GND_6), U1.138 (GND); also elsewhere on the board
unnamed: L2.1, R40.2
VDDOUT: C3.1, C4.1, C5.1, C6.1, C7.1, C17.1, C20.1, C22.1, L1.1, U1.3 (VDDOUT), U1.29 (VDDCORE_2), U1.33 (VDDCORE_3), U1.50 (VDDCORE_4), U1.81 (VDDCORE_5), U1.107 (VDDCORE), U1.139 (VDDTUMIC)
VDDPLL: C15.1, L1.2, U1.123 (VDDPLL)
VDDPLLUSB: C16.1, L2.2, U1.143 (VDDPLLUSB)
VREFN: U1.8 (VREFN)
VREFP: U1.9 (VREFP)

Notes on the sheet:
can this 1A regulator supply enough current?? (w/o getting too hot)
do we want an tiny cap/battery backup to try and save the 1k backup sdram in the case of a bus brownout during flight? and do we want an RTC?

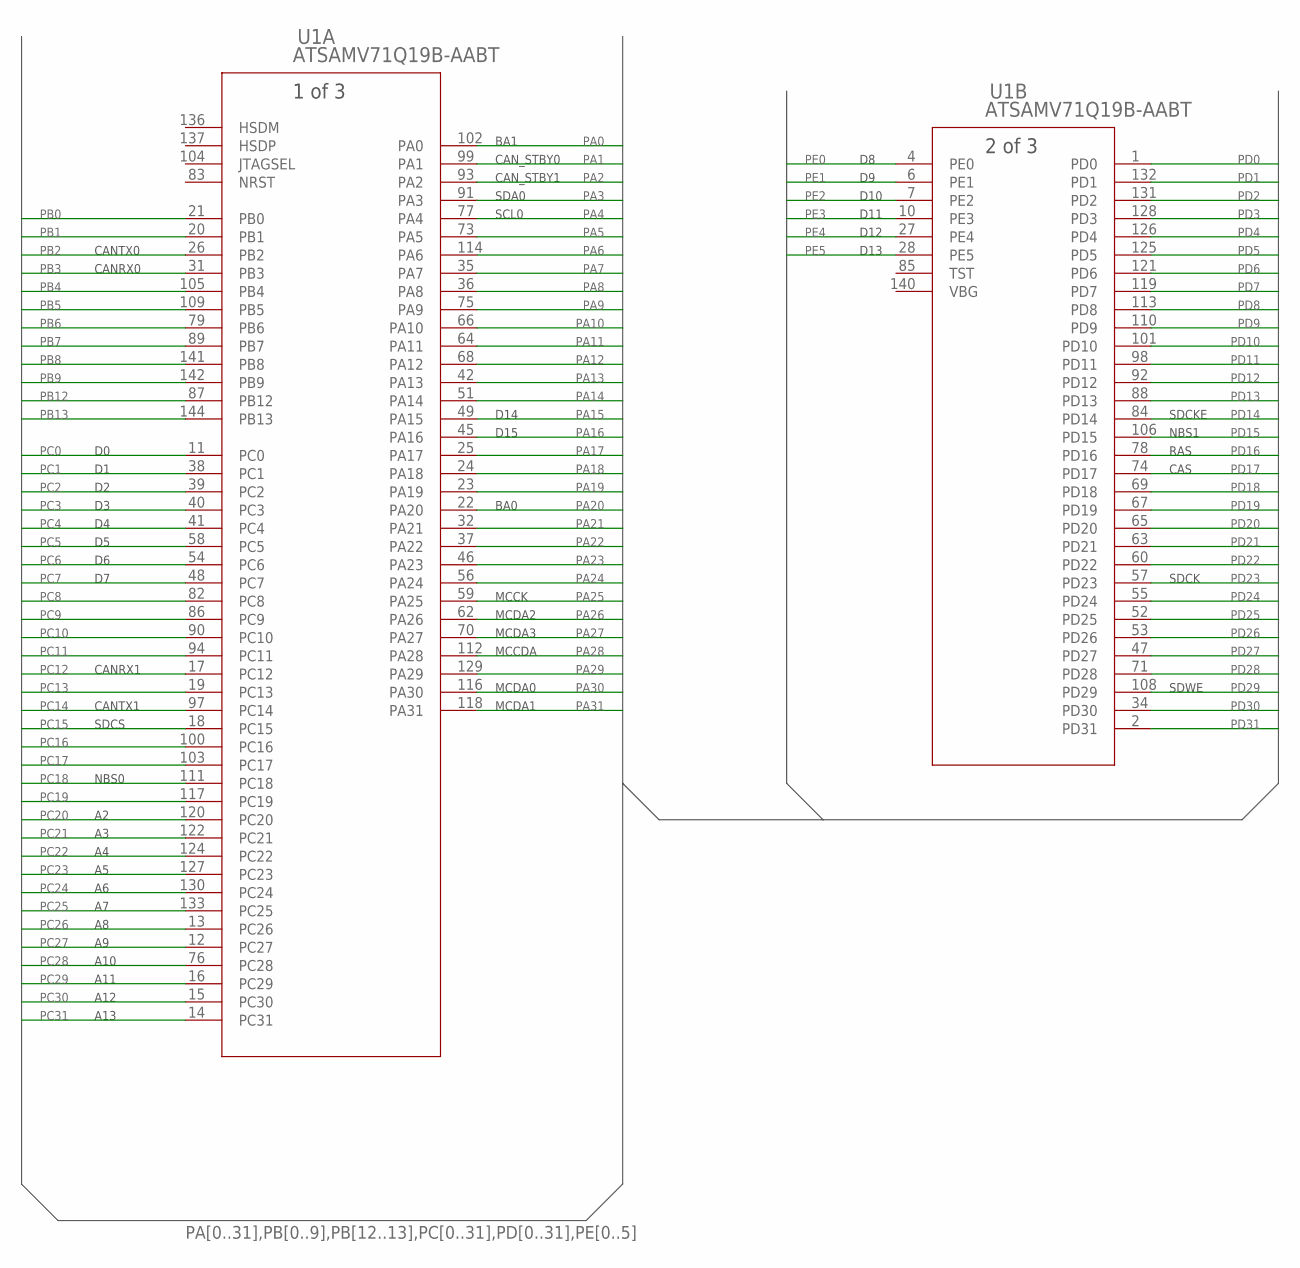
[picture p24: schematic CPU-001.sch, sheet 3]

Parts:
U1: ATSAMV71Q19B-AABT; LQFP144_20X20MC

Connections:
PA0: U1.102 (PA0); also elsewhere on the board
PA1: U1.99 (PA1); also elsewhere on the board
PA2: U1.93 (PA2); also elsewhere on the board
PA3: U1.91 (PA3); also elsewhere on the board
PA4: U1.77 (PA4); also elsewhere on the board
PA5: U1.73 (PA5)
PA6: U1.114 (PA6)
PA7: U1.35 (PA7)
PA8: U1.36 (PA8)
PA9: U1.75 (PA9)
PA10: U1.66 (PA10)
PA11: U1.64 (PA11)
PA12: U1.68 (PA12)
PA13: U1.42 (PA13)
PA14: U1.51 (PA14)
PA15: U1.49 (PA15); also elsewhere on the board
PA16: U1.45 (PA16); also elsewhere on the board
PA17: U1.25 (PA17)
PA18: U1.24 (PA18)
PA19: U1.23 (PA19)
PA20: U1.22 (PA20); also elsewhere on the board
PA21: U1.32 (PA21)
PA22: U1.37 (PA22)
PA23: U1.46 (PA23)
PA24: U1.56 (PA24)
PA25: U1.59 (PA25); also elsewhere on the board
PA26: U1.62 (PA26); also elsewhere on the board
PA27: U1.70 (PA27); also elsewhere on the board
PA28: U1.112 (PA28); also elsewhere on the board
PA29: U1.129 (PA29)
PA30: U1.116 (PA30); also elsewhere on the board
PA31: U1.118 (PA31); also elsewhere on the board
PB0: U1.21 (PB0)
PB1: U1.20 (PB1)
PB2: U1.26 (PB2); also elsewhere on the board
PB3: U1.31 (PB3); also elsewhere on the board
PB4: U1.105 (PB4)
PB5: U1.109 (PB5)
PB6: U1.79 (PB6)
PB7: U1.89 (PB7)
PB8: U1.141 (PB8)
PB9: U1.142 (PB9)
PB12: U1.87 (PB12)
PB13: U1.144 (PB13)
PC0: U1.11 (PC0); also elsewhere on the board
PC1: U1.38 (PC1); also elsewhere on the board
PC2: U1.39 (PC2); also elsewhere on the board
PC3: U1.40 (PC3); also elsewhere on the board
PC4: U1.41 (PC4); also elsewhere on the board
PC5: U1.58 (PC5); also elsewhere on the board
PC6: U1.54 (PC6); also elsewhere on the board
PC7: U1.48 (PC7); also elsewhere on the board
PC8: U1.82 (PC8)
PC9: U1.86 (PC9)
PC10: U1.90 (PC10)
PC11: U1.94 (PC11)
PC12: U1.17 (PC12); also elsewhere on the board
PC13: U1.19 (PC13)
PC14: U1.97 (PC14); also elsewhere on the board
PC15: U1.18 (PC15); also elsewhere on the board
PC16: U1.100 (PC16)
PC17: U1.103 (PC17)
PC18: U1.111 (PC18); also elsewhere on the board
PC19: U1.117 (PC19)
PC20: U1.120 (PC20); also elsewhere on the board
PC21: U1.122 (PC21); also elsewhere on the board
PC22: U1.124 (PC22); also elsewhere on the board
PC23: U1.127 (PC23); also elsewhere on the board
PC24: U1.130 (PC24); also elsewhere on the board
PC25: U1.133 (PC25); also elsewhere on the board
PC26: U1.13 (PC26); also elsewhere on the board
PC27: U1.12 (PC27); also elsewhere on the board
PC28: U1.76 (PC28); also elsewhere on the board
PC29: U1.16 (PC29); also elsewhere on the board
PC30: U1.15 (PC30); also elsewhere on the board
PC31: U1.14 (PC31); also elsewhere on the board
PD0: U1.1 (PD0)
PD1: U1.132 (PD1)
PD2: U1.131 (PD2)
PD3: U1.128 (PD3)
PD4: U1.126 (PD4)
PD5: U1.125 (PD5)
PD6: U1.121 (PD6)
PD7: U1.119 (PD7)
PD8: U1.113 (PD8)
PD9: U1.110 (PD9)
PD10: U1.101 (PD10)
PD11: U1.98 (PD11)
PD12: U1.92 (PD12)
PD13: U1.88 (PD13)
PD14: U1.84 (PD14); also elsewhere on the board
PD15: U1.106 (PD15); also elsewhere on the board
PD16: U1.78 (PD16); also elsewhere on the board
PD17: U1.74 (PD17); also elsewhere on the board
PD18: U1.69 (PD18)
PD19: U1.67 (PD19)
PD20: U1.65 (PD20)
PD21: U1.63 (PD21)
PD22: U1.60 (PD22)
PD23: U1.57 (PD23); also elsewhere on the board
PD24: U1.55 (PD24)
PD25: U1.52 (PD25)
PD26: U1.53 (PD26)
PD27: U1.47 (PD27)
PD28: U1.71 (PD28)
PD29: U1.108 (PD29); also elsewhere on the board
PD30: U1.34 (PD30)
PD31: U1.2 (PD31)
PE0: U1.4 (PE0); also elsewhere on the board
PE1: U1.6 (PE1); also elsewhere on the board
PE2: U1.7 (PE2); also elsewhere on the board
PE3: U1.10 (PE3); also elsewhere on the board
PE4: U1.27 (PE4); also elsewhere on the board
PE5: U1.28 (PE5); also elsewhere on the board
VREFN: U1.8 (VREFN)
VREFP: U1.9 (VREFP)

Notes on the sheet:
NBS0
A10
A11
A12
A13
BA0
BA1
D10
D11
D12
D13
D14
D15
SDCK
SDCKE
NBS1
SDWE
CAS
RAS
SDCS
CANTX0
CANRX0
CANTX1
CANRX1
MCCK
MCDA2
MCDA3
MCCDA
MCDA0
MCDA1
CAN_STBY0
CAN_STBY1
SCL0
SDA0

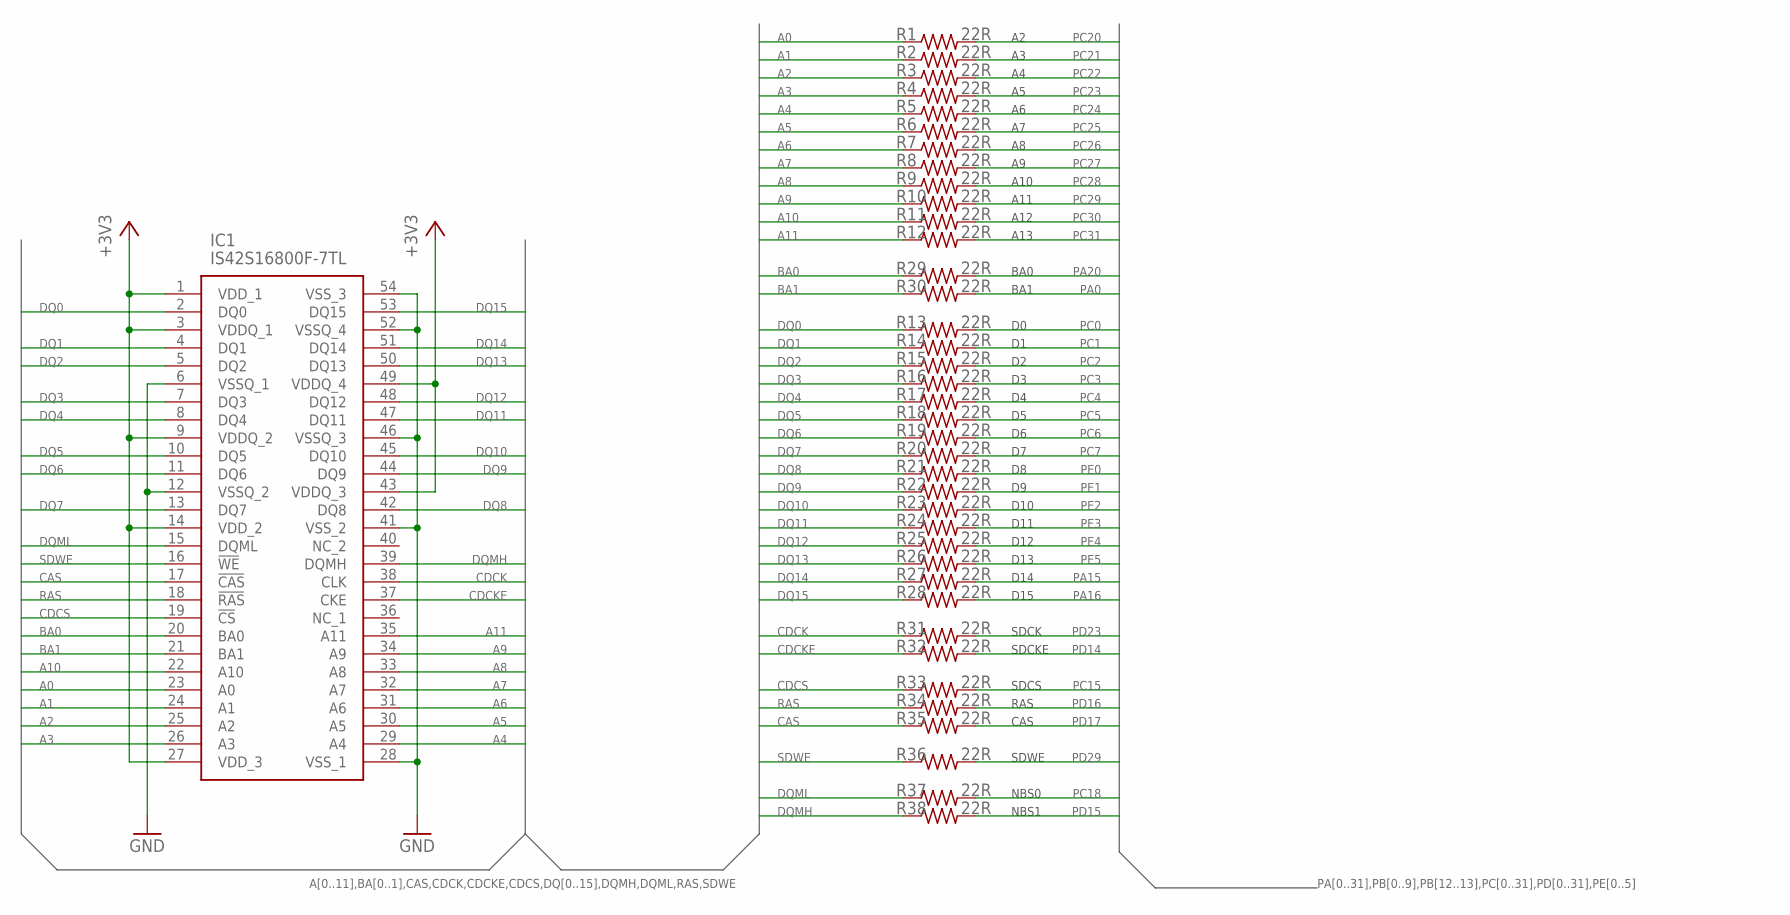
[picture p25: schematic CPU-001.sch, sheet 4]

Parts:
IC1: IS42S16800F-7TL; SOP80P1176X120-54N
R1, R2, R3, R4, R5, R6, R7, R8, R9, R10, R11, R12, R13, R14, R15, R16, R17, R18, R19, R20, R21, R22, R23, R24, R25, R26, R27, R28, R29, R30, R31, R32, R33, R34, R35, R36, R37, R38: 22R; R0402

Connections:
+3V3: IC1.1 (VDD_1), IC1.3 (VDDQ_1), IC1.9 (VDDQ_2), IC1.14 (VDD_2), IC1.27 (VDD_3), IC1.43 (VDDQ_3), IC1.49 (VDDQ_4); also elsewhere on the board
A0: IC1.23 (A0), R1.1
A1: IC1.24 (A1), R2.1
A2: IC1.25 (A2), R3.1
A3: IC1.26 (A3), R4.1
A4: IC1.29 (A4), R5.1
A5: IC1.30 (A5), R6.1
A6: IC1.31 (A6), R7.1
A7: IC1.32 (A7), R8.1
A8: IC1.33 (A8), R9.1
A9: IC1.34 (A9), R10.1
A10: IC1.22 (A10), R11.1
A11: IC1.35 (A11), R12.1
BA0: IC1.20 (BA0), R29.1
BA1: IC1.21 (BA1), R30.1
CAS: IC1.17 (!CAS), R35.1
CDCK: IC1.38 (CLK), R31.1
CDCKE: IC1.37 (CKE), R32.1
CDCS: IC1.19 (!CS), R33.1
DQ0: IC1.2 (DQ0), R13.1
DQ1: IC1.4 (DQ1), R14.1
DQ2: IC1.5 (DQ2), R15.1
DQ3: IC1.7 (DQ3), R16.1
DQ4: IC1.8 (DQ4), R17.1
DQ5: IC1.10 (DQ5), R18.1
DQ6: IC1.11 (DQ6), R19.1
DQ7: IC1.13 (DQ7), R20.1
DQ8: IC1.42 (DQ8), R21.1
DQ9: IC1.44 (DQ9), R22.1
DQ10: IC1.45 (DQ10), R23.1
DQ11: IC1.47 (DQ11), R24.1
DQ12: IC1.48 (DQ12), R25.1
DQ13: IC1.50 (DQ13), R26.1
DQ14: IC1.51 (DQ14), R27.1
DQ15: IC1.53 (DQ15), R28.1
DQMH: IC1.39 (DQMH), R38.1
DQML: IC1.15 (DQML), R37.1
GND: IC1.6 (VSSQ_1), IC1.12 (VSSQ_2), IC1.28 (VSS_1), IC1.41 (VSS_2), IC1.46 (VSSQ_3), IC1.52 (VSSQ_4), IC1.54 (VSS_3); also elsewhere on the board
PA0: R30.2; also elsewhere on the board
PA15: R27.2; also elsewhere on the board
PA16: R28.2; also elsewhere on the board
PA20: R29.2; also elsewhere on the board
PC0: R13.2; also elsewhere on the board
PC1: R14.2; also elsewhere on the board
PC2: R15.2; also elsewhere on the board
PC3: R16.2; also elsewhere on the board
PC4: R17.2; also elsewhere on the board
PC5: R18.2; also elsewhere on the board
PC6: R19.2; also elsewhere on the board
PC7: R20.2; also elsewhere on the board
PC15: R33.2; also elsewhere on the board
PC18: R37.2; also elsewhere on the board
PC20: R1.2; also elsewhere on the board
PC21: R2.2; also elsewhere on the board
PC22: R3.2; also elsewhere on the board
PC23: R4.2; also elsewhere on the board
PC24: R5.2; also elsewhere on the board
PC25: R6.2; also elsewhere on the board
PC26: R7.2; also elsewhere on the board
PC27: R8.2; also elsewhere on the board
PC28: R9.2; also elsewhere on the board
PC29: R10.2; also elsewhere on the board
PC30: R11.2; also elsewhere on the board
PC31: R12.2; also elsewhere on the board
PD14: R32.2; also elsewhere on the board
PD15: R38.2; also elsewhere on the board
PD16: R34.2; also elsewhere on the board
PD17: R35.2; also elsewhere on the board
PD23: R31.2; also elsewhere on the board
PD29: R36.2; also elsewhere on the board
PE0: R21.2; also elsewhere on the board
PE1: R22.2; also elsewhere on the board
PE2: R23.2; also elsewhere on the board
PE3: R24.2; also elsewhere on the board
PE4: R25.2; also elsewhere on the board
PE5: R26.2; also elsewhere on the board
RAS: IC1.18 (!RAS), R34.1
SDWE: IC1.16 (!WE), R36.1

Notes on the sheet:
A10
A11
A12
A13
BA0
BA1
D10
D11
D12
D13
D14
D15
SDCK
SDCKE
NBS1
NBS0
SDWE
CAS
RAS
SDCS

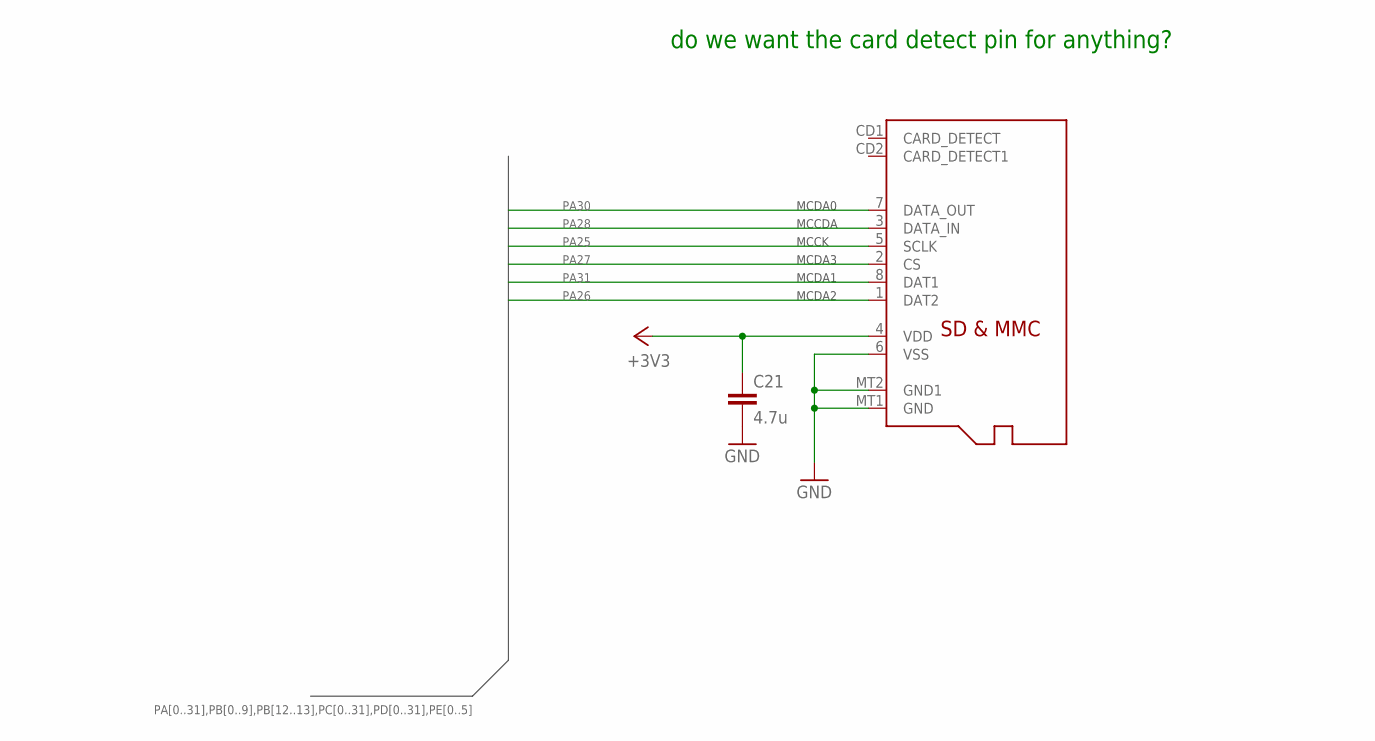
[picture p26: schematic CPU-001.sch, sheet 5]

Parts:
C21: 4.7u; C0805
U$5: MICROSD; MICROSD_

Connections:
+3V3: C21.1, U$5.4 (VDD); also elsewhere on the board
GND: C21.2, U$5.6 (VSS), U$5.MT1 (GND), U$5.MT2 (GND1); also elsewhere on the board
PA25: U$5.5 (SCLK); also elsewhere on the board
PA26: U$5.1 (DAT2); also elsewhere on the board
PA27: U$5.2 (CS); also elsewhere on the board
PA28: U$5.3 (DATA_IN); also elsewhere on the board
PA30: U$5.7 (DATA_OUT); also elsewhere on the board
PA31: U$5.8 (DAT1); also elsewhere on the board

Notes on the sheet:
MCCK
MCDA3
MCDA1
MCDA2
MCCDA
MCDA0
do we want the card detect pin for anything?

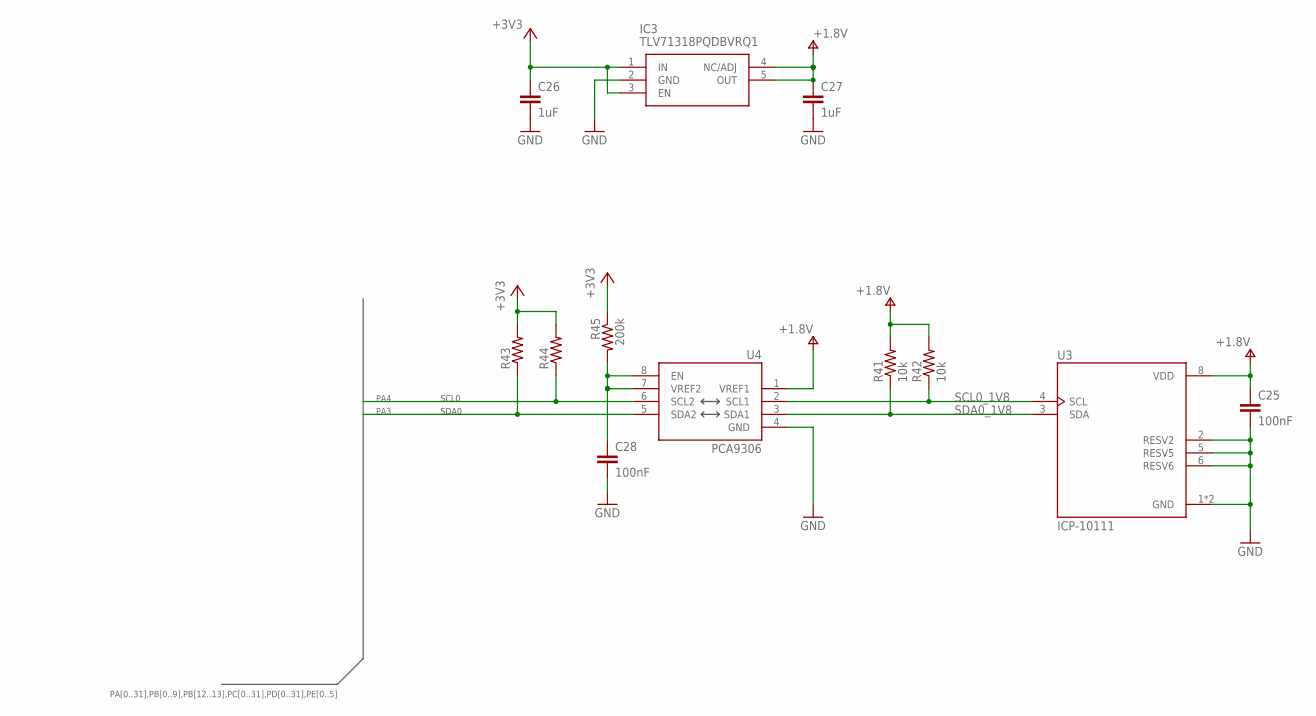
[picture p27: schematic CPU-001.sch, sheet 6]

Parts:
C25, C28: 100nF; C0402
C26, C27: 1uF; C0402
IC3: TLV71318PQDBVRQ1; SOT95P280X100-5N
R41, R42: 10k; R0402
R43, R44: R-US_R0402; R0402
R45: 200k; R0402
U3: ICP-10111; PSON65P250X200X100-8N
U4: PCA9306; PCA9306DC

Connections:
+1.8V: C25.1, C27.1, IC3.4 (NC/ADJ), IC3.5 (OUT), R41.2, R42.2, U3.8 (VDD), U4.1 (VREF1)
+3V3: C26.1, IC3.1 (IN), IC3.3 (EN), R43.2, R44.2, R45.1; also elsewhere on the board
GND: C25.2, C26.2, C27.2, C28.2, IC3.2 (GND), U3.1 (GND), U3.2 (RESV2), U3.5 (RESV5), U3.6 (RESV6), U3.7 (GND), U4.4 (GND); also elsewhere on the board
unnamed: C28.1, R45.2, U4.7 (VREF2), U4.8 (EN)
PA3: R43.1, U4.5 (SDA2); also elsewhere on the board
PA4: R44.1, U4.6 (SCL2); also elsewhere on the board
SCL0_1V8: R42.1, U3.4 (SCL), U4.2 (SCL1)
SDA0_1V8: R41.1, U3.3 (SDA), U4.3 (SDA1)

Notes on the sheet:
SDA0
SCL0

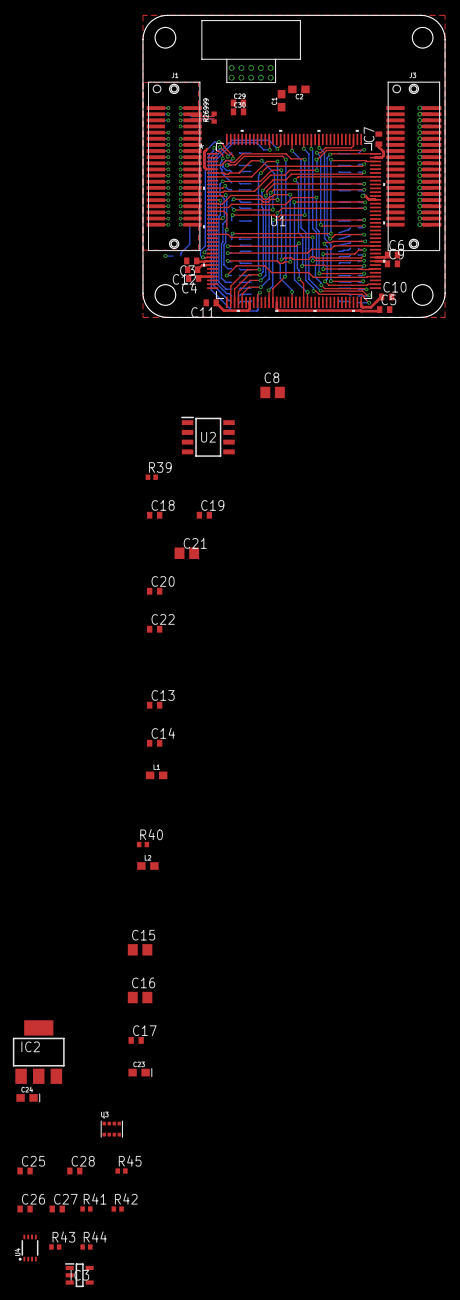
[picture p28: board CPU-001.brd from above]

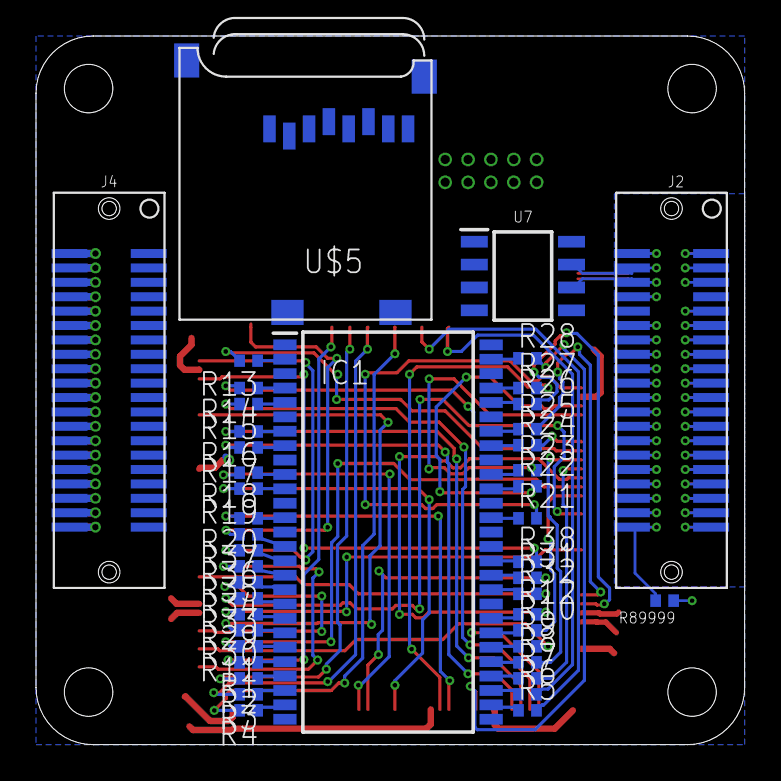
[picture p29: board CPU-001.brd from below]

Board: 2 copper layers, 39.4 x 39.4 mm, 93 parts (44 on the bottom side), 135 nets.

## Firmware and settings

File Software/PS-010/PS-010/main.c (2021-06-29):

#include <atmel_start.h>
#include "hpl_adc_config.h"
#include "mps_utils.h"
#include "canard.h"
#include "o1heap.h"
//#include "bsp_can.h"

#define adc_pres 1000000
#define ADC_REF_VOLTAGE 2.0480
#if CONF_ADC_0_RESSEL == 0x0
  #define ADC_RESOLUTION (1<<12)
#elif CONF_ADC_0_RESSEL == 0x1
  #define ADC_RESOLUTION (1<<16)
#elif CONF_ADC_0_RESSEL == 0x2
  #define ADC_RESOLUTION (1<<10)
#elif CONF_ADC_0_RESSEL == 0x3
  #define ADC_RESOLUTION (1<<8)
#else
  #error "CONF_ADC_0_RESSEL NOT DEFINED"
#endif

#define O1_HEAP_START 0x20001000
#define O1_HEAP_SIZE 0x1000


#define ADC_CH_VBAT_VMON		0x00	// PA02 - AIN0
#define ADC_CH_12V_INT_VMON		0x04	// PA04 - AIN4
#define ADC_CH_5V_BT_VMON		0x05	// PA05 - AIN5
#define ADC_CH_5V_VMON			0x06	// PA06 - AIN6
#define ADC_CH_5V_BT_INT_VMON	0x07	// PA07 - AIN7
#define ADC_CH_5V_INT_VMON		0x08	// PA08 - AIN8
#define ADC_CH_12V_VMON			0x09	// PA09 - AIN9
#define ADC_CH_5V_IMON			0x0A	// PA10 - AIN10
#define ADC_CH_12V_IMON			0x0B	// PA11 - AIN11

void print_adc_voltage(uint8_t channel, int numerator, int demoninator, char unit)
{
		uint8_t buffer[2];
		WAIT_APPROX_MILLIS(10);
		_adc_sync_set_inputs(&ADC_0, channel, 0x18, 0);
		adc_sync_enable_channel(&ADC_0, 0);
		adc_sync_read_channel(&ADC_0, 0, buffer, 2);
		//adc_sync_disable_channel(&ADC_0, channel);
		unsigned int val = (buffer[1]<<8)+(buffer[0]);
		unsigned int voltage_uV = val*(ADC_REF_VOLTAGE*adc_pres/ADC_RESOLUTION);
		unsigned int votlage_converted = voltage_uV*numerator/demoninator;
		printf("ADC CH %u: %u, %u, %u.%u %c\r\n", channel, val, voltage_uV, (unsigned int)(votlage_converted/adc_pres),(unsigned int)(votlage_converted/1000-(adc_pres/1000)*(votlage_converted/adc_pres)), unit);
}

O1HeapInstance* heap = NULL;
/*
bool pleaseTransmit(CanardFrame* txf)
{
	
}*/
/*
void empty(CanardInstance* const ins)
{
	for (const CanardFrame* txf = NULL; (txf = canardTxPeek(&ins)) != NULL;)  // Look at the top of the TX queue.
	{
		if ((0U == txf->timestamp_usec) || (txf->timestamp_usec > getCurrentMicroseconds()))  // Check the deadline.
		{
			if (!pleaseTransmit(txf))              // Send the frame. Redundant interfaces may be used here.
			{
				break;                             // If the driver is busy, break and retry later.
			}
		}
		canardTxPop(&ins);                         // Remove the frame from the queue after it's transmitted.
		ins.memory_free(&ins, (CanardFrame*)txf);  // Deallocate the dynamic memory afterwards.
	}
}*/

static void* memAllocate(CanardInstance* const ins, const size_t amount)
{
	(void) ins;
	return o1heapAllocate(heap, amount);
}

static void memFree(CanardInstance* const ins, void* const pointer)
{
	(void) ins;
	o1heapFree(heap, pointer);
}

int main(void)
{
	unsigned int loop_count = 0;
	/* Initializes MCU, drivers and middleware */
	atmel_start_init();
		
	printf("init done\r\n");
	printf("adc res: %i, %i\r\n",CONF_ADC_0_RESSEL,ADC_RESOLUTION);
	WAIT_APPROX_MILLIS(100);
	int32_t temp;
	temp_sync_enable(&TEMPERATURE_SENSOR_0);
	/* Replace with your application code */
	
	printf("O1Heap allocating memory at: 0x%x size: 0x%x bytes...\r\n", O1_HEAP_START, O1_HEAP_SIZE);
	
	//heap = o1heapInit(O1_HEAP_START, O1_HEAP_SIZE, NULL, NULL);
	
	if(heap == NULL) {
		printf("O1Heap memory allocation FAILED\r\n");
	} else {
		printf("O1Heap memory allocation done\r\n");
	}
	
	//CanardInstance ins = canardInit(&memAllocate, &memFree);
	//ins.mtu_bytes = CANARD_MTU_CAN_CLASSIC;  // Defaults to 64 (CAN FD); here we select Classic CAN.
	//ins.node_id   = 42;                      // Defaults to anonymous; can be set up later at any point.
	
	while (1) {
		if(loop_count>0) {
			gpio_set_pin_level(EN_5V, 1);
			gpio_set_pin_level(EN_12V, 1);
		}
		
		print_adc_voltage(ADC_CH_VBAT_VMON, 250, 10, 'V');
		//print_adc_voltage(ADC_CH_5V_BT_INT_VMON, 56, 20, 'V');
		print_adc_voltage(ADC_CH_5V_BT_VMON, 56, 20, 'V');
		//print_adc_voltage(ADC_CH_5V_INT_VMON, 56, 20, 'V');
		print_adc_voltage(ADC_CH_5V_VMON, 56, 20, 'V');
		print_adc_voltage(ADC_CH_5V_IMON, 2000, 1, 'm');
		//print_adc_voltage(ADC_CH_12V_INT_VMON, 130, 20, 'V');
		print_adc_voltage(ADC_CH_12V_VMON, 130, 20, 'V');
		print_adc_voltage(ADC_CH_12V_IMON, 2000, 1, 'm');
		temp_sync_read(&TEMPERATURE_SENSOR_0, &temp);
		printf("temp: %ul\r\n", temp);
		
		WAIT_APPROX_MILLIS(1000);
		printf("end loop %u\r\n",loop_count);
		WAIT_APPROX_MILLIS(100);
		loop_count++;
	}
}

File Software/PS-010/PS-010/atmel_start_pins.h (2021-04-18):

/*
 * Code generated from Atmel Start.
 *
 * This file will be overwritten when reconfiguring your Atmel Start project.
 * Please copy examples or other code you want to keep to a separate file
 * to avoid losing it when reconfiguring.
 */
#ifndef ATMEL_START_PINS_H_INCLUDED
#define ATMEL_START_PINS_H_INCLUDED

#include <hal_gpio.h>

// SAMC21 has 9 pin functions

#define GPIO_PIN_FUNCTION_A 0
#define GPIO_PIN_FUNCTION_B 1
#define GPIO_PIN_FUNCTION_C 2
#define GPIO_PIN_FUNCTION_D 3
#define GPIO_PIN_FUNCTION_E 4
#define GPIO_PIN_FUNCTION_F 5
#define GPIO_PIN_FUNCTION_G 6
#define GPIO_PIN_FUNCTION_H 7
#define GPIO_PIN_FUNCTION_I 8

#define CTRL_SYNC GPIO(GPIO_PORTA, 0)
#define PA02 GPIO(GPIO_PORTA, 2)
#define PA03 GPIO(GPIO_PORTA, 3)
#define PA04 GPIO(GPIO_PORTA, 4)
#define PA05 GPIO(GPIO_PORTA, 5)
#define PA06 GPIO(GPIO_PORTA, 6)
#define PA07 GPIO(GPIO_PORTA, 7)
#define PA08 GPIO(GPIO_PORTA, 8)
#define PA09 GPIO(GPIO_PORTA, 9)
#define PA10 GPIO(GPIO_PORTA, 10)
#define PA11 GPIO(GPIO_PORTA, 11)
#define DETECT_A GPIO(GPIO_PORTA, 12)
#define DETECT_B GPIO(GPIO_PORTA, 13)
#define PA16 GPIO(GPIO_PORTA, 16)
#define PA17 GPIO(GPIO_PORTA, 17)
#define PG_5V_BT GPIO(GPIO_PORTA, 18)
#define PG_5V GPIO(GPIO_PORTA, 19)
#define PG_12V GPIO(GPIO_PORTA, 20)
#define EN_12V GPIO(GPIO_PORTA, 21)
#define EN_5V_BT GPIO(GPIO_PORTA, 22)
#define EN_5V GPIO(GPIO_PORTA, 23)
#define P_GOODn GPIO(GPIO_PORTA, 27)
#define CAN0_STBY GPIO(GPIO_PORTA, 28)
#define PB22 GPIO(GPIO_PORTB, 22)
#define PB23 GPIO(GPIO_PORTB, 23)

#endif // ATMEL_START_PINS_H_INCLUDED

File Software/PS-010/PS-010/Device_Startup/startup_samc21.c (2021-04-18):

/**
 * \file
 *
 * \brief gcc starttup file for SAMC21
 *
 * Copyright (c) 2018 Microchip Technology Inc.
 *
 * \asf_license_start
 *
 * \page License
 *
 * SPDX-License-Identifier: Apache-2.0
 *
 * Licensed under the Apache License, Version 2.0 (the "License"); you may
 * not use this file except in compliance with the License.
 * You may obtain a copy of the Licence at
 * 
 * http://www.apache.org/licenses/LICENSE-2.0
 * 
 * Unless required by applicable law or agreed to in writing, software
 * distributed under the License is distributed on an AS IS BASIS, WITHOUT
 * WARRANTIES OR CONDITIONS OF ANY KIND, either express or implied.
 * See the License for the specific language governing permissions and
 * limitations under the License.
 *
 * \asf_license_stop
 *
 */

#include "samc21.h"

/* Initialize segments */
extern uint32_t _sfixed;
extern uint32_t _efixed;
extern uint32_t _etext;
extern uint32_t _srelocate;
extern uint32_t _erelocate;
extern uint32_t _szero;
extern uint32_t _ezero;
extern uint32_t _sstack;
extern uint32_t _estack;

/** \cond DOXYGEN_SHOULD_SKIP_THIS */
int main(void);
/** \endcond */

void __libc_init_array(void);

/* Default empty handler */
void Dummy_Handler(void);

/* Cortex-M0+ core handlers */
void NonMaskableInt_Handler  ( void ) __attribute__ ((weak, alias("Dummy_Handler")));
void HardFault_Handler       ( void ) __attribute__ ((weak, alias("Dummy_Handler")));
void SVCall_Handler          ( void ) __attribute__ ((weak, alias("Dummy_Handler")));
void PendSV_Handler          ( void ) __attribute__ ((weak, alias("Dummy_Handler")));
void SysTick_Handler         ( void ) __attribute__ ((weak, alias("Dummy_Handler")));

/* Peripherals handlers */
void SYSTEM_Handler          ( void ) __attribute__ ((weak, alias("Dummy_Handler"))); /* MCLK, OSC32KCTRL, OSCCTRL, PAC, PM, SUPC, TAL */
void WDT_Handler             ( void ) __attribute__ ((weak, alias("Dummy_Handler")));
void RTC_Handler             ( void ) __attribute__ ((weak, alias("Dummy_Handler")));
void EIC_Handler             ( void ) __attribute__ ((weak, alias("Dummy_Handler")));
void FREQM_Handler           ( void ) __attribute__ ((weak, alias("Dummy_Handler")));
#ifdef ID_TSENS
void TSENS_Handler           ( void ) __attribute__ ((weak, alias("Dummy_Handler")));
#endif
void NVMCTRL_Handler         ( void ) __attribute__ ((weak, alias("Dummy_Handler")));
void DMAC_Handler            ( void ) __attribute__ ((weak, alias("Dummy_Handler")));
void EVSYS_Handler           ( void ) __attribute__ ((weak, alias("Dummy_Handler")));
void SERCOM0_Handler         ( void ) __attribute__ ((weak, alias("Dummy_Handler")));
void SERCOM1_Handler         ( void ) __attribute__ ((weak, alias("Dummy_Handler")));
void SERCOM2_Handler         ( void ) __attribute__ ((weak, alias("Dummy_Handler")));
void SERCOM3_Handler         ( void ) __attribute__ ((weak, alias("Dummy_Handler")));
#ifdef ID_SERCOM4
void SERCOM4_Handler         ( void ) __attribute__ ((weak, alias("Dummy_Handler")));
#endif
#ifdef ID_SERCOM5
void SERCOM5_Handler         ( void ) __attribute__ ((weak, alias("Dummy_Handler")));
#endif
#ifdef ID_CAN0
void CAN0_Handler            ( void ) __attribute__ ((weak, alias("Dummy_Handler")));
#endif
#ifdef ID_CAN1
void CAN1_Handler            ( void ) __attribute__ ((weak, alias("Dummy_Handler")));
#endif
void TCC0_Handler            ( void ) __attribute__ ((weak, alias("Dummy_Handler")));
#ifdef ID_TCC1
void TCC1_Handler            ( void ) __attribute__ ((weak, alias("Dummy_Handler")));
#endif
#ifdef ID_TCC2
void TCC2_Handler            ( void ) __attribute__ ((weak, alias("Dummy_Handler")));
#endif
void TC0_Handler             ( void ) __attribute__ ((weak, alias("Dummy_Handler")));
void TC1_Handler             ( void ) __attribute__ ((weak, alias("Dummy_Handler")));
void TC2_Handler             ( void ) __attribute__ ((weak, alias("Dummy_Handler")));
void TC3_Handler             ( void ) __attribute__ ((weak, alias("Dummy_Handler")));
void TC4_Handler             ( void ) __attribute__ ((weak, alias("Dummy_Handler")));
#ifdef ID_ADC0
void ADC0_Handler            ( void ) __attribute__ ((weak, alias("Dummy_Handler")));
#endif
#ifdef ID_ADC1
void ADC1_Handler            ( void ) __attribute__ ((weak, alias("Dummy_Handler")));
#endif
#ifdef ID_AC
void AC_Handler              ( void ) __attribute__ ((weak, alias("Dummy_Handler")));
#endif
#ifdef ID_DAC
void DAC_Handler             ( void ) __attribute__ ((weak, alias("Dummy_Handler")));
#endif
#ifdef ID_SDADC
void SDADC_Handler           ( void ) __attribute__ ((weak, alias("Dummy_Handler")));
#endif
#ifdef ID_PTC
void PTC_Handler             ( void ) __attribute__ ((weak, alias("Dummy_Handler")));
#endif
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

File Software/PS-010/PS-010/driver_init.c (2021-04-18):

/*
 * Code generated from Atmel Start.
 *
 * This file will be overwritten when reconfiguring your Atmel Start project.
 * Please copy examples or other code you want to keep to a separate file
 * to avoid losing it when reconfiguring.
 */

#include "driver_init.h"
#include <peripheral_clk_config.h>
#include <utils.h>
#include <hal_init.h>

#include <hpl_adc_base.h>

struct can_async_descriptor CAN_0;

struct adc_sync_descriptor ADC_0;

struct usart_sync_descriptor DEBUG_UART;

struct temp_sync_descriptor TEMPERATURE_SENSOR_0;

void ADC_0_PORT_init(void)
{

	// Disable digital pin circuitry
	gpio_set_pin_direction(PA02, GPIO_DIRECTION_OFF);

	gpio_set_pin_function(PA02, PINMUX_PA02B_ADC0_AIN0);

	// Disable digital pin circuitry
	gpio_set_pin_direction(PA04, GPIO_DIRECTION_OFF);

	gpio_set_pin_function(PA04, PINMUX_PA04B_ADC0_AIN4);

	// Disable digital pin circuitry
	gpio_set_pin_direction(PA05, GPIO_DIRECTION_OFF);

	gpio_set_pin_function(PA05, PINMUX_PA05B_ADC0_AIN5);

	// Disable digital pin circuitry
	gpio_set_pin_direction(PA06, GPIO_DIRECTION_OFF);

	gpio_set_pin_function(PA06, PINMUX_PA06B_ADC0_AIN6);

	// Disable digital pin circuitry
	gpio_set_pin_direction(PA07, GPIO_DIRECTION_OFF);

	gpio_set_pin_function(PA07, PINMUX_PA07B_ADC0_AIN7);

	// Disable digital pin circuitry
	gpio_set_pin_direction(PA08, GPIO_DIRECTION_OFF);

	gpio_set_pin_function(PA08, PINMUX_PA08B_ADC0_AIN8);

	// Disable digital pin circuitry
	gpio_set_pin_direction(PA09, GPIO_DIRECTION_OFF);

	gpio_set_pin_function(PA09, PINMUX_PA09B_ADC0_AIN9);

	// Disable digital pin circuitry
	gpio_set_pin_direction(PA10, GPIO_DIRECTION_OFF);

	gpio_set_pin_function(PA10, PINMUX_PA10B_ADC0_AIN10);

	// Disable digital pin circuitry
	gpio_set_pin_direction(PA11, GPIO_DIRECTION_OFF);

	gpio_set_pin_function(PA11, PINMUX_PA11B_ADC0_AIN11);

	// Disable digital pin circuitry
	gpio_set_pin_direction(PA03, GPIO_DIRECTION_OFF);

	gpio_set_pin_function(PA03, PINMUX_PA03B_ADC0_VREFP);
}

void ADC_0_CLOCK_init(void)
{
	hri_mclk_set_APBCMASK_ADC0_bit(MCLK);
	hri_gclk_write_PCHCTRL_reg(GCLK, ADC0_GCLK_ID, CONF_GCLK_ADC0_SRC | (1 << GCLK_PCHCTRL_CHEN_Pos));
}

void ADC_0_init(void)
{
	ADC_0_CLOCK_init();
	ADC_0_PORT_init();
	adc_sync_init(&ADC_0, ADC0, _adc_get_adc_sync());
}

void DEBUG_UART_PORT_init(void)
{

	gpio_set_pin_function(PA16, PINMUX_PA16D_SERCOM3_PAD0);

	gpio_set_pin_function(PA17, PINMUX_PA17D_SERCOM3_PAD1);
}

void DEBUG_UART_CLOCK_init(void)
{
	hri_gclk_write_PCHCTRL_reg(GCLK, SERCOM3_GCLK_ID_CORE, CONF_GCLK_SERCOM3_CORE_SRC | (1 << GCLK_PCHCTRL_CHEN_Pos));
	hri_gclk_write_PCHCTRL_reg(GCLK, SERCOM3_GCLK_ID_SLOW, CONF_GCLK_SERCOM3_SLOW_SRC | (1 << GCLK_PCHCTRL_CHEN_Pos));
	hri_mclk_set_APBCMASK_SERCOM3_bit(MCLK);
}

void DEBUG_UART_init(void)
{
	DEBUG_UART_CLOCK_init();
	usart_sync_init(&DEBUG_UART, SERCOM3, (void *)NULL);
	DEBUG_UART_PORT_init();
}

void CAN_0_PORT_init(void)
{

	gpio_set_pin_function(PB23, PINMUX_PB23G_CAN0_RX);

	gpio_set_pin_function(PB22, PINMUX_PB22G_CAN0_TX);
}
/**
 * \brief CAN initialization function
 *
 * Enables CAN peripheral, clocks and initializes CAN driver
 */
void CAN_0_init(void)
{
	hri_mclk_set_AHBMASK_CAN0_bit(MCLK);
	hri_gclk_write_PCHCTRL_reg(GCLK, CAN0_GCLK_ID, CONF_GCLK_CAN0_SRC | (1 << GCLK_PCHCTRL_CHEN_Pos));
	can_async_init(&CAN_0, CAN0);
	CAN_0_PORT_init();
}

void TEMPERATURE_SENSOR_0_CLOCK_init(void)
{
	hri_mclk_set_APBAMASK_TSENS_bit(MCLK);

	hri_gclk_write_PCHCTRL_reg(GCLK, TSENS_GCLK_ID, CONF_GCLK_TSENS_SRC | (1 << GCLK_PCHCTRL_CHEN_Pos));
}

void TEMPERATURE_SENSOR_0_init(void)
{
	TEMPERATURE_SENSOR_0_CLOCK_init();
	temp_sync_init(&TEMPERATURE_SENSOR_0, TSENS);
}

void system_init(void)
{
	init_mcu();

	// GPIO on PA00

	// Set pin direction to input
	gpio_set_pin_direction(CTRL_SYNC, GPIO_DIRECTION_IN);

	gpio_set_pin_pull_mode(CTRL_SYNC,
	                       // <y> Pull configuration
	                       // <id> pad_pull_config
	                       // <GPIO_PULL_OFF"> Off
	                       // <GPIO_PULL_UP"> Pull-up
	                       // <GPIO_PULL_DOWN"> Pull-down
	                       GPIO_PULL_DOWN);

	gpio_set_pin_function(CTRL_SYNC, GPIO_PIN_FUNCTION_OFF);

	// GPIO on PA12

	// Set pin direction to input
	gpio_set_pin_direction(DETECT_A, GPIO_DIRECTION_IN);

	gpio_set_pin_pull_mode(DETECT_A,
	                       // <y> Pull configuration
	                       // <id> pad_pull_config
	                       // <GPIO_PULL_OFF"> Off
	                       // <GPIO_PULL_UP"> Pull-up
	                       // <GPIO_PULL_DOWN"> Pull-down
	                       GPIO_PULL_UP);

	gpio_set_pin_function(DETECT_A, GPIO_PIN_FUNCTION_OFF);

	// GPIO on PA13

	// Set pin direction to input
	gpio_set_pin_direction(DETECT_B, GPIO_DIRECTION_IN);

	gpio_set_pin_pull_mode(DETECT_B,
	                       // <y> Pull configuration
	                       // <id> pad_pull_config
	                       // <GPIO_PULL_OFF"> Off
	                       // <GPIO_PULL_UP"> Pull-up
	                       // <GPIO_PULL_DOWN"> Pull-down
	                       GPIO_PULL_UP);

	gpio_set_pin_function(DETECT_B, GPIO_PIN_FUNCTION_OFF);

	// GPIO on PA18

	// Set pin direction to input
	gpio_set_pin_direction(PG_5V_BT, GPIO_DIRECTION_IN);

	gpio_set_pin_pull_mode(PG_5V_BT,
	                       // <y> Pull configuration
	                       // <id> pad_pull_config
	                       // <GPIO_PULL_OFF"> Off
	                       // <GPIO_PULL_UP"> Pull-up
	                       // <GPIO_PULL_DOWN"> Pull-down
	                       GPIO_PULL_OFF);

	gpio_set_pin_function(PG_5V_BT, GPIO_PIN_FUNCTION_OFF);

	// GPIO on PA19

	// Set pin direction to input
	gpio_set_pin_direction(PG_5V, GPIO_DIRECTION_IN);

	gpio_set_pin_pull_mode(PG_5V,
	                       // <y> Pull configuration
	                       // <id> pad_pull_config
	                       // <GPIO_PULL_OFF"> Off
	                       // <GPIO_PULL_UP"> Pull-up
	                       // <GPIO_PULL_DOWN"> Pull-down
	                       GPIO_PULL_OFF);

	gpio_set_pin_function(PG_5V, GPIO_PIN_FUNCTION_OFF);

	// GPIO on PA20

	// Set pin direction to input
	gpio_set_pin_direction(PG_12V, GPIO_DIRECTION_IN);

	gpio_set_pin_pull_mode(PG_12V,
	                       // <y> Pull configuration
	                       // <id> pad_pull_config
	                       // <GPIO_PULL_OFF"> Off
	                       // <GPIO_PULL_UP"> Pull-up
	                       // <GPIO_PULL_DOWN"> Pull-down
	                       GPIO_PULL_OFF);

	gpio_set_pin_function(PG_12V, GPIO_PIN_FUNCTION_OFF);

	// GPIO on PA21

	gpio_set_pin_level(EN_12V,
	                   // <y> Initial level
	                   // <id> pad_initial_level
	                   // <false"> Low
	                   // <true"> High
	                   false);

	// Set pin direction to output
	gpio_set_pin_direction(EN_12V, GPIO_DIRECTION_OUT);

	gpio_set_pin_function(EN_12V, GPIO_PIN_FUNCTION_OFF);
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

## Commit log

2020-02-10 added current files
    [BOB-001.brd, BOB-001.sch, CPU-001.brd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]
2020-02-10 update processor
    [PS-001.csv]
2020-02-10 added pin mappings
    [Pin Mappings.ods]
2020-02-10 added SAMC21 to PS-001 tab of pin mappings
    [Pin Mappings.ods]
2020-02-10 add PS pin mapping
    [Pin Mappings.ods]
2020-02-10 more work on CPU-001
    [CPU-001.brd, CPU-001.sch, Pin Mappings.ods]
2020-02-10 updated sch with atsamC21G - brd needs work
    [PS-001.brd, PS-001.sch]
2020-02-12 updating voltage rails, should we get rid of
    [PS-001.brd, PS-001.sch]
2020-02-12 added altimeter.. working through schematic slowly...
    [CPU-001.brd, CPU-001.sch, Pin Mappings.ods]
2020-02-12 added some note to ps-001 sch
    [PS-001.sch]
2020-02-17 fixed supply ORing
    [PS-001.brd, PS-001.sch]
2020-02-17 add template files
    [template.brd, template.sch]
2020-02-23 added pullup and swdclk and changed some cap packages
    [PS-001.brd, PS-001.sch, Pin Mappings.ods]
2020-04-29 fixed power rail naming in template and added inventor drawing
    [Outline.ipt, template.brd, template.sch]
2020-04-29 updates to CPU-001 and DBG-001
    [CPU-001.brd, CPU-001.sch, DBG-001.brd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]
2020-04-29 updates to IO-001
    [IO-001.brd, IO-001.sch]
2020-04-29 added a new debug board designed for pogopins
    [DBG-002.brd, DBG-002.sch]
2020-04-29 updates to ps-001
    [PS-001 - Copy.brd, PS-001.sch]
2020-09-20 create TMP-001 Altium files
    [Sheet1.SchDoc, TMP-001.PrjPcb]
2020-09-21 added connectors to library...
    [TMP-001.PrjPcb]
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2020-09-23 sims and some other stuff...
    [Pin Mappings.ods, template.brd, template.sch]
2020-09-28 progess on TMP-001...
    [Outline.dxf, Pin Mappings.ods, Sheet1.SchDoc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]
2020-09-28 test pcb file
    [PCB1.PcbDoc]
2020-09-28 test 2
    [TMP-001.PcbDoc]
2020-09-28 add some new footprints
    [TMP-001.PrjPcb]
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2020-10-04 progress on TMP-001. lost some work :(
    [Pin Mappings.ods, Sheet1.SchDoc, Sheet2.SchDoc]
2020-10-10 working on part placement. sch is done.
    [Sheet1.SchDoc, Sheet2.SchDoc, TMP-001.PrjPcb]
2020-10-11 routing the board
    [Sheet1.SchDoc, Sheet2.SchDoc]
2020-10-19 working on routing. still need to fix some rules and polys
    [Sheet1.SchDoc]
2020-10-19 add vbat bootstrap\
    [Sheet1.SchDoc]
2020-10-19 updated outline
    [Outline.dxf, Outline.ipt, Sheet1.SchDoc]
2020-10-19 tmp-001 done? i should add a PN/SN to the silk
    [Outline.ipt, Sheet1.SchDoc]
2020-10-20 added more notes, some P/N silkscreen, and licenseing
    [Sheet1.SchDoc, Sheet2.SchDoc]
2020-10-20 remove obsolete template
    [Outline.ipt, template.brd, template.sch]
2020-11-03 DBG-040 ready for release...
    [DBG-040.PrjPcb, DBG-040.step, Sheet1.SchDoc]
2020-11-12 spacer board work
    [DBG-040.PrjPcb, Sheet1.SchDoc]
2020-11-15 started DBG-010
    [DBG-010.PrjPcb, Sheet1.SchDoc, Sheet2.SchDoc]
2020-11-15 fixed name and started current sense board
    [DBG-020.PrjPcb, Sheet1.SchDoc, Sheet2.SchDoc]
2020-11-27 simulated +5V and +12V input filters
    [+12V Input Filter Simulation Results.csv, +5V Input Filter Simulation Results.csv]
2020-11-27 progress on PS-010!
    [PS-010 Main.PrjPcb, Sheet1.SchDoc, Sheet2.SchDoc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]
2020-12-02 board is looking good so far...
    [PCB1.PcbDoc, PS-010 Aux.PrjPcb, PS-010 Main.PrjPcb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]
2020-12-04 board is nearing completion, so that's kinda cool
    [Sheet2.SchDoc, Sheet6.SchDoc]
2020-12-05 added Unit Price information and finished routing
    [Sheet1.SchDoc, Sheet2.SchDoc, Sheet3.SchDoc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]
2020-12-07 work on BAT-010
    [BAT-010.PcbDoc, BAT-010.PrjPcb, PS-010.PrjPcb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]
2020-12-09 idk. who knows
    [Sheet2.SchDoc]
2020-12-20 removed old files
    [BAT-010.PcbDoc, DBG-010.PcbDoc, DBG-010.PrjPcb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]
2020-12-21 added source follower buffer to P_GOOD
    [DBG-010.PcbDoc, Sheet2.SchDoc]
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2020-12-25 housekeeping... also changed from B.1 to B... im too lazy to deal with minor revs
    [Sheet1.SchDoc, TMP-010.PrjPcb]
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2021-01-01 tuning up params and improving auto gen module list script
    [DBG-010.PrjPcb]
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2021-01-02 cleaning up old files and starting to port CPU-010 to alitum
    [CPU-001.brd, CPU-001.sch, CPU-010.PcbDoc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]
2021-01-02 working on ATSAM V71 power and data pinouts
    [Pin Mappings.ods, Sheet2.SchDoc, Sheet3.SchDoc]
2021-01-02 added ethernet to CPU-010 pinout
    [Pin Mappings.ods, Sheet2.SchDoc]
2021-01-03 added note about series resistors on 3.3V bus singals and a warning about backpowering the 3.3V rail from P_GOOD
    [CPU-010.PcbDoc, CPU-010.PrjPcb, Connectors.SchDoc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]
2021-01-04 working on ethernet interface
    [CPU-010.PrjPcb, Connectors.SchDoc, Ethernet.SchDoc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]
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2021-01-05 added magnetics to libary. The Altium Library Loader seems buggy on Altium 21
    [Ethernet.SchDoc]
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2021-01-08 added molex mez connector
    [Ethernet.SchDoc]
2021-01-10 fixed standoffs
2021-01-10 CPU-010 and CPUEX-010 work
    [CPU-010.PcbDoc, CPU-010.PrjPcb, CPUEX-010.PcbDoc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]
2021-01-10 more work on DBG-010
    [CPUEX-010.PcbDoc, Sheet1.SchDoc, Sheet2.SchDoc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]
2021-01-11 DBG-010 is about ready to order
    [CPUEX-010.PrjPcb, DBG-010.PrjPcb, Pin Mappings.ods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]
2021-01-11 fixed P23 pinout
    [Sheet1.SchDoc]
2021-01-12 added DBG-020 and DBG-030 for pogo pins
    [DBG-020.PcbDoc, DBG-030.PcbDoc, DBG-030.PrjPcb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]
2021-01-13 DBG-020 and DBG-030 ready for release:
    [DBG-002.brd, DBG-002.sch, DBG-020.PcbDoc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]
2021-01-13 ready for a pre-release of PS-010.
    [PS-010.PrjPcb, PS-010.xlsx, Sheet1.SchDoc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]
2021-01-16 DBG-010 ready for release
    [DBG-010.PrjPcb, Sheet1.SchDoc, Sheet2.SchDoc]
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2022-05-21 work on test bench stuff
    [Sheet1.SchDoc, Sheet3.SchDoc]

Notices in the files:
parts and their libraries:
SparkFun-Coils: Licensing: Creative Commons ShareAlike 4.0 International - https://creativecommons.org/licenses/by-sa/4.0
